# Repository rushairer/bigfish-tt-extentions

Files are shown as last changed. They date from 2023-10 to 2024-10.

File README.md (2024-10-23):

# 大鱼 TT 增强包

## 关于本项目

`大鱼TT` 是 B 站 UP`大鱼DIY`在 2023 年发布的一款 CoreXY 结构的开源 3D 打印机方案。

大家都习惯把资料在 QQ 群里讨论分享，但是不方便检索，所以我创建了这个项目，把组装过程中用到的资源，一点点收集到这里。同时也欢迎其他机友补充和提交资料。

### 简单分享下我这个零基础小白在装机过程中遇到的坑。

前前后后半个多月，学到了很多知识，感谢大鱼 DIY 给我们带来的这款大鱼 TT，感谢群里曾经帮助过我的各位朋友。

首先说 BOM 表。本来是想一键下单的，但是由于产能原因，有些店铺没货。没办法只能自己照单抓药一个个在各种店铺下单买，单品型号可能有一些差异，于是遇到了一些奇奇怪怪的问题。

我有一个树莓派 3b，装了 LED3.5 触摸屏，一直闲着。所以就打算用 BOM 里提到的树莓派+八爪鱼的方案。后来我才知道大鱼他是用小政主板做的，兼容性会比较好。八爪鱼主板遇到的一些问题基本上都是在大鱼群和八爪鱼的群里各位大佬的帮助下解决的，在这里再次表示感谢。

然后说说“拓竹”的挤出机，是所谓的 2.0 版本，尾端和散热块的地方有螺丝片加固的那款，风扇固定需要两颗 M2.5\*16 的螺丝，这个 BOM 里没有提。

再就是接近开关。一开始我是用的 BOM 链接买的 24V 的 NPN 接近开关，配的八爪鱼 1.1 主板。这个主板端是 PNP 的，所以 24V 的 NPN 不能直接用，除非自己接个下拉电阻，我不会。听说 Pro 的板子可以用 NPN。于是我又买了一块八爪鱼 Pro，实测发现即使接了 NPN 跳脚，也不能用。后来我买了一个 5V 的 NPN 常闭，可以在 1.1 和 Pro 上用，需要在 Pin 前面加上“~”。

~~关于这个接近开关问题我多提点吧，毕竟当时卡了我好几天。先说 24VNPN 的时候，我分别测试了 24V，12V，5V。在 24V 时接触金属 5.8V，不接触 3V。在 12V 时，接触金属 2.xV，不接触 1.2V。那我猜在 5V 时，接触金属应该 1.xV，不接触金属 0.xV，就可以一个 1 一个 0 两个电平形成开关信号了吧？可惜这个接近开关的额定电压是 6V-36V，在 5V 下不工作。后来我购买了 5V 的 NPN 证实了这一猜测。至于背后的原理，等我回头复习一下电路知识，重新整理。这里做个备忘。~~

6 张图来弄明白为什么八爪鱼 1.1 主板不能直接用 NPN 的接近开关，和如何解决这个问题。

图一、图二分别是 NPN 接近开关和 PNP 接近开关的原理。
通过查看八爪鱼 1.1 的电路图得知，如图四那样，接近开关的信号引脚和 GND 接了一个光耦开关。通过图三可以看到，NPN 接近开关信号引脚和 GND 之间电压很低，所以不能完全打开光耦。
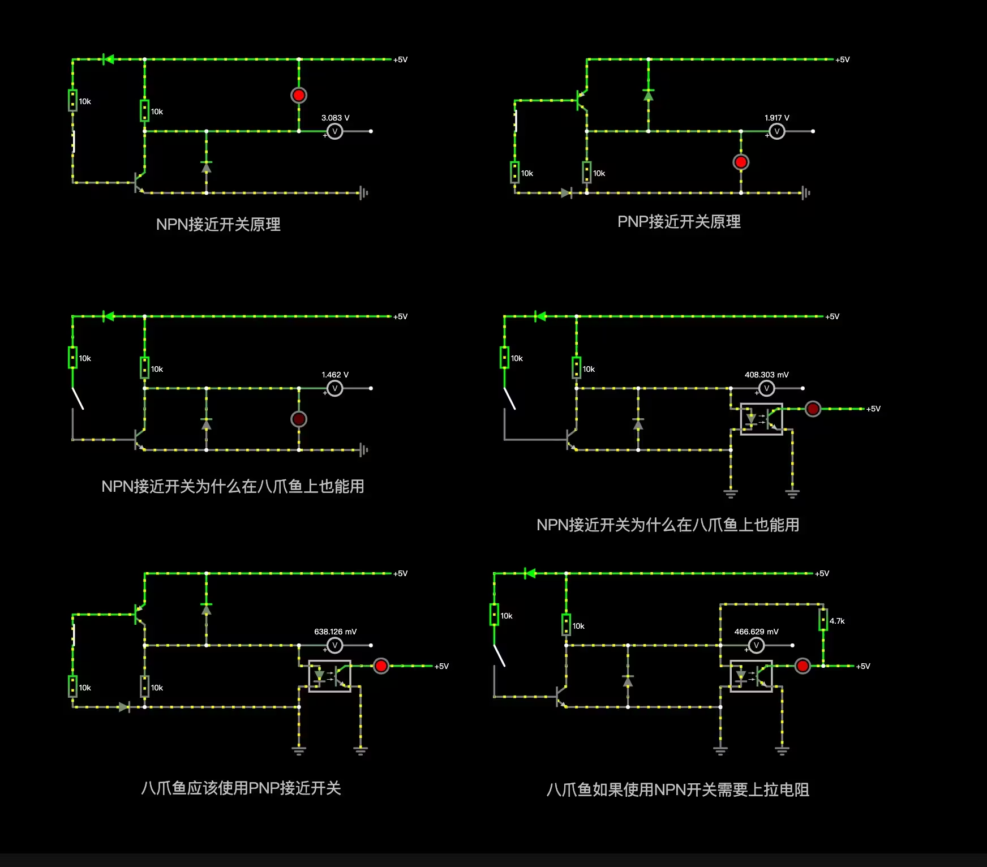
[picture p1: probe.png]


看八爪鱼的原理图，100K 下拉电阻是 NC 状态，也就没有焊。所以需要加  ~  来内部下拉，也就是 ~PB7。当光耦不能完全打开时，~PB7 的电压高低跳变就可能不稳定，所以表现出来就是不能工作或者测量不准确。具体的情况就需要看具体型号的接近开关的额定电压情况了。
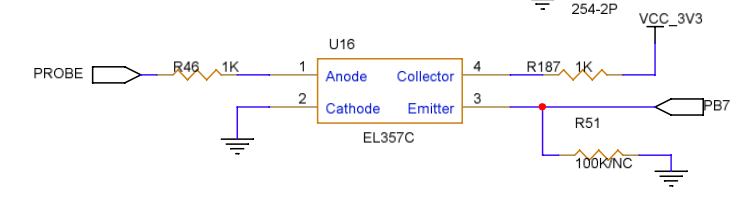
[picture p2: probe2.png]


所以我们应该用 PNP 型接近开关 或者 NPN 接近开关把信号引脚接一个上拉电阻。

~~2023 年 10 月 16 日 00:20:50 获得的好消息，24V NPN 接近开关可以在八爪鱼上使用了，接线方法：正负极接电源正负极，信号 PIN 还是接 Probe 的信号 PIN 就可以用了~~

接近开关的热飘非常明显，首层打印不稳定，所以后来我决定试试 Klicky 方案。Klicky 的开源方案有很多，我是用的 https://github.com/tanaes/whopping_Voron_mods/tree/main/pcb_klicky 的方案。停靠坞使用 MG90s/SG90 舵机，（不要用 MG996 等大电流舵机，主板带不动）。我单独开一篇来分享一下 Klicky+舵机的配置过程。

还有各种电线，是否用 CanBus，XH2.54 的端子等等细节问题。太碎了，实在是懒得一条条列举了，而且我相信列出来大家也未必一条条仔细看。还是有啥问题去群里问各位网友吧。

对了还有那个热床 MOS，如果不是大功率的热床，不需要买的。

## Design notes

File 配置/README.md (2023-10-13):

# 我的配置

## TODO

    目前没有详细说明，仅供参考。

    我把打印范围改成 300x300x300的了，周围余了5mm，不是因为Klicky，只是觉得热床很难100%四个顶点对齐，不如留点余量。

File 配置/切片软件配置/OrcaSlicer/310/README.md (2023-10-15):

# 我的配置

## 310x310x310 可以跑满吗？

我觉得我的组装精度很难保证 310x310 的四个顶点都能对应上，所以我还是改成 300x300x300 的可用区域了。

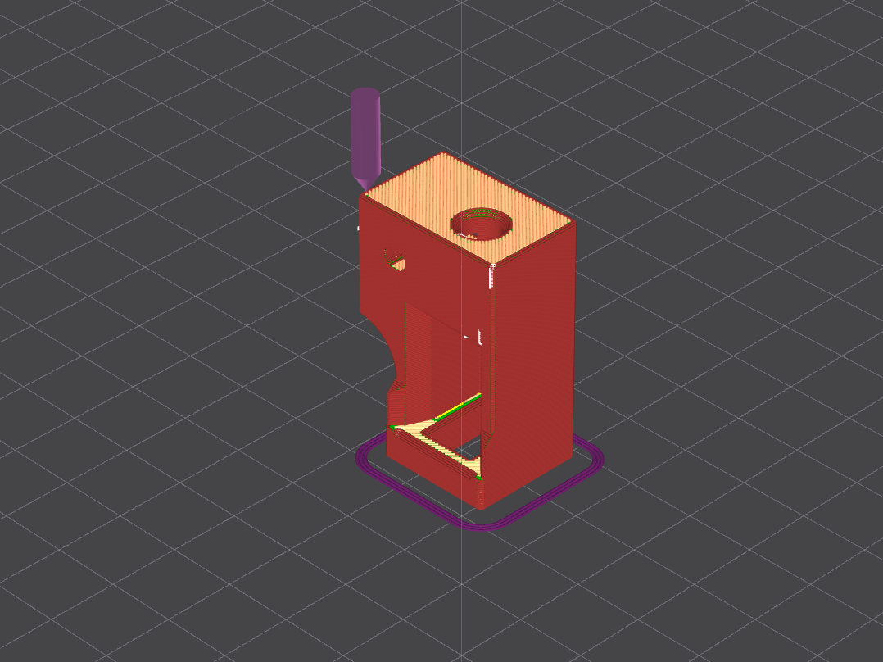
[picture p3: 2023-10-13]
扩展/Klicky/PCB Klicky/支架/切片方式-不需要支撑.png

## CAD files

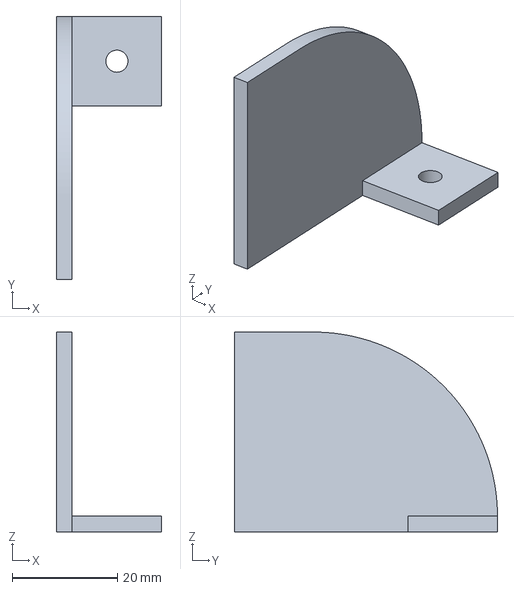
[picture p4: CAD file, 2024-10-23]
Klicky Dock 舵机扭转角度限位.3mf
20.0 x 50.0 x 38.0 mm

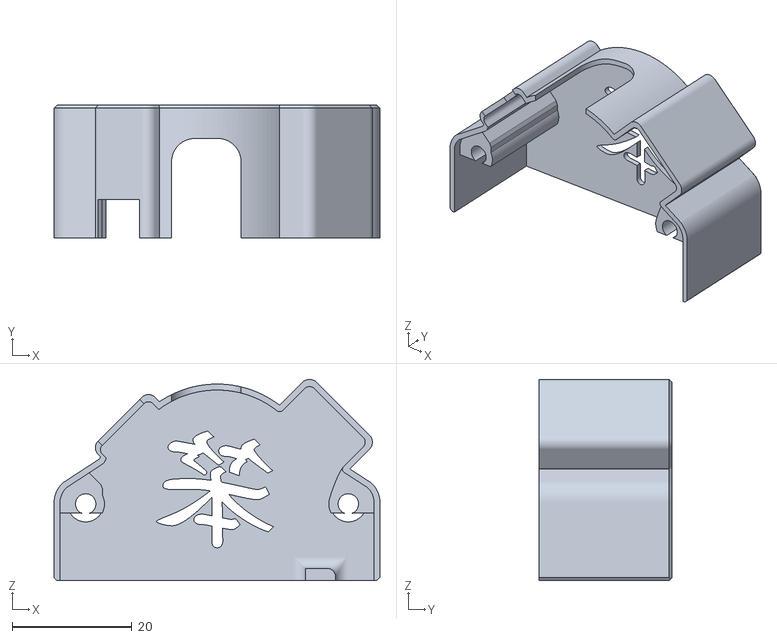
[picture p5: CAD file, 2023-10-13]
扩展/CanBus/Can 外壳.stl
54.4 x 22.2 x 33.6

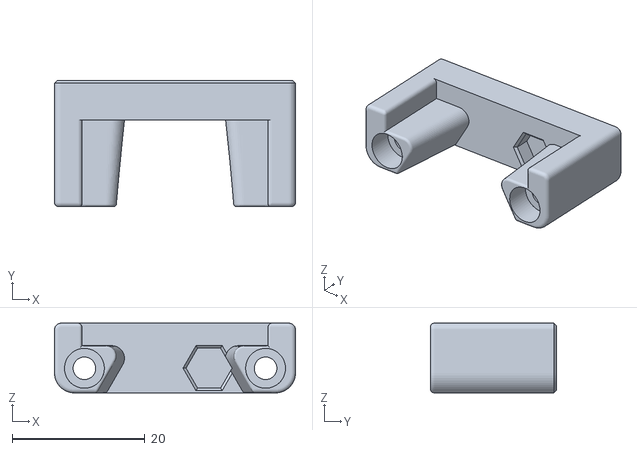
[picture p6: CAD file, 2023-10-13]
扩展/Klicky/PCB Klicky/PCB方案用的东西/停靠坞.stl
36.3 x 19.0 x 10.5

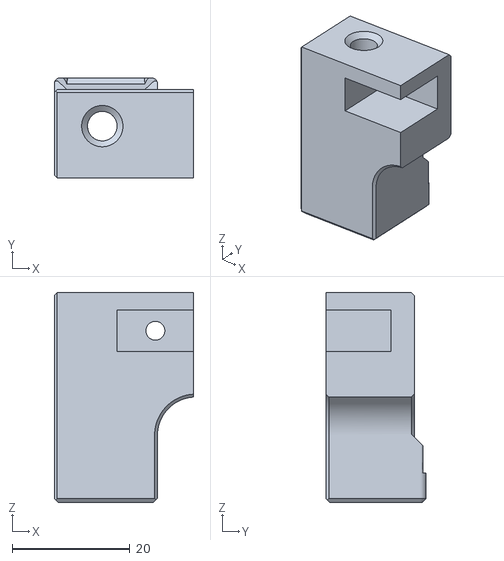
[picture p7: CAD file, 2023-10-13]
扩展/Klicky/PCB Klicky/支架/固定架-固定在原接近开关的位置.stl
23.6 x 17.0 x 35.6

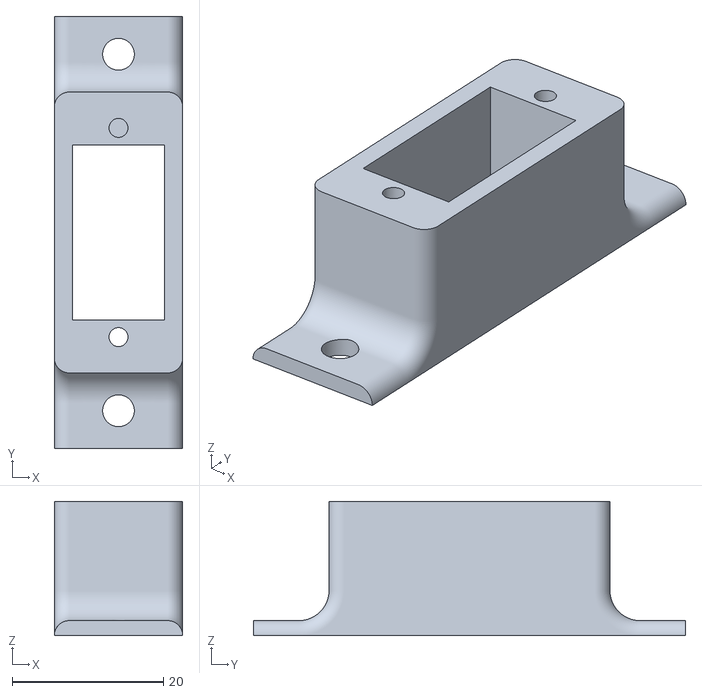
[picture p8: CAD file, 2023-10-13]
扩展/Klicky/PCB Klicky/舵机/固定在热床型材的方案/MG90s_SG90舵机固定架.stl
17.0 x 57.2 x 17.8

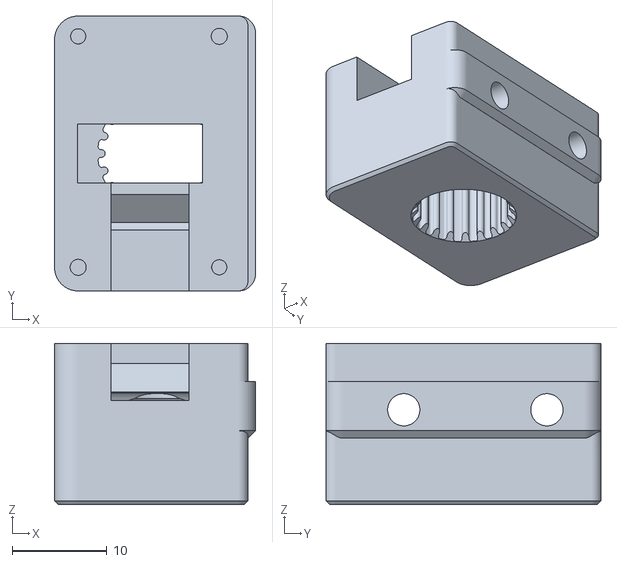
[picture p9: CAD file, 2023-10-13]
扩展/Z限位/Z轴限位PCB安装座.stl
21.2 x 29.0 x 17.0

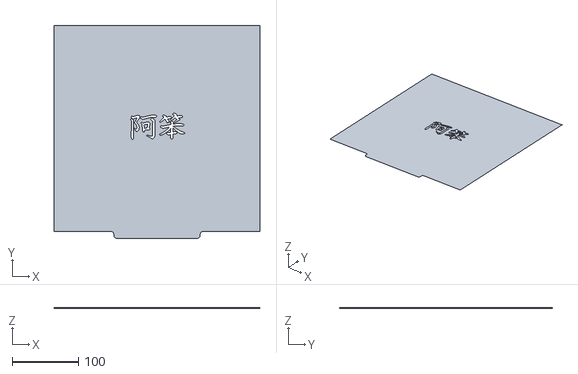
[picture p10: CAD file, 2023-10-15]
扩展/其他/310x310平台板模型.stl
310.0 x 320.0 x 0.1

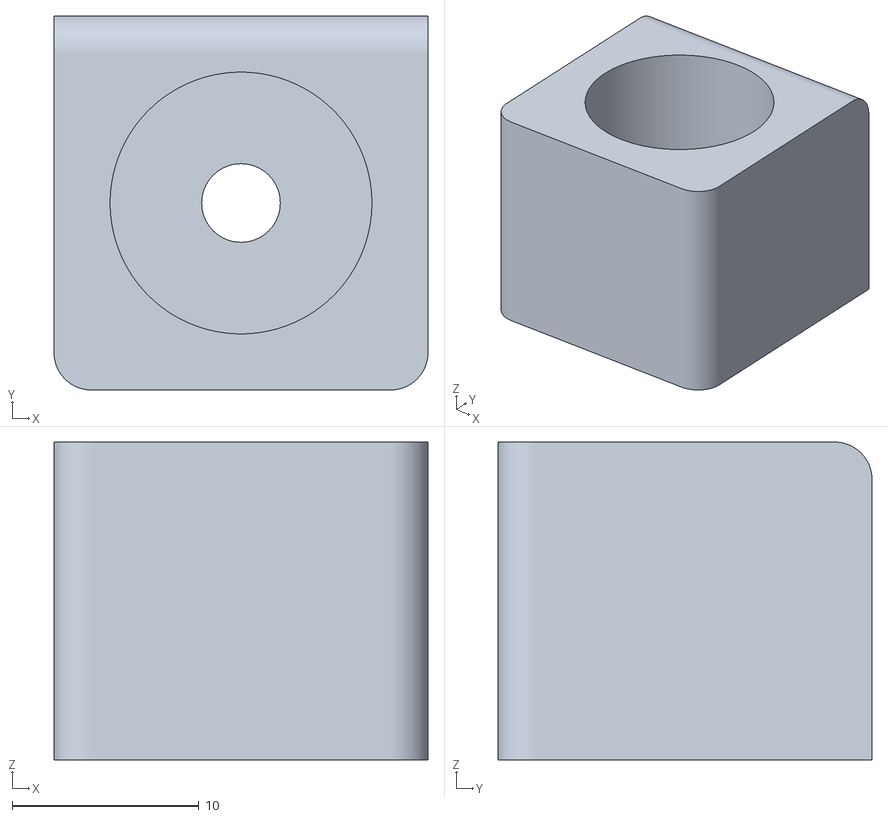
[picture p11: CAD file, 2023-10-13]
扩展/自动擦嘴/热床平台板边缘对齐辅助装置.stl
20.0 x 20.0 x 17.0

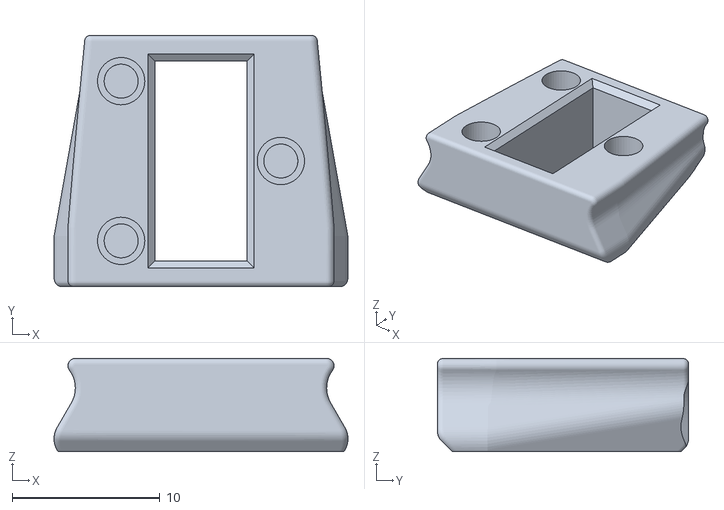
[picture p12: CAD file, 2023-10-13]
扩展/Klicky/PCB Klicky/PCB方案用的东西/热熔螺丝版探针固定架.stl
19.9 x 17.0 x 6.30

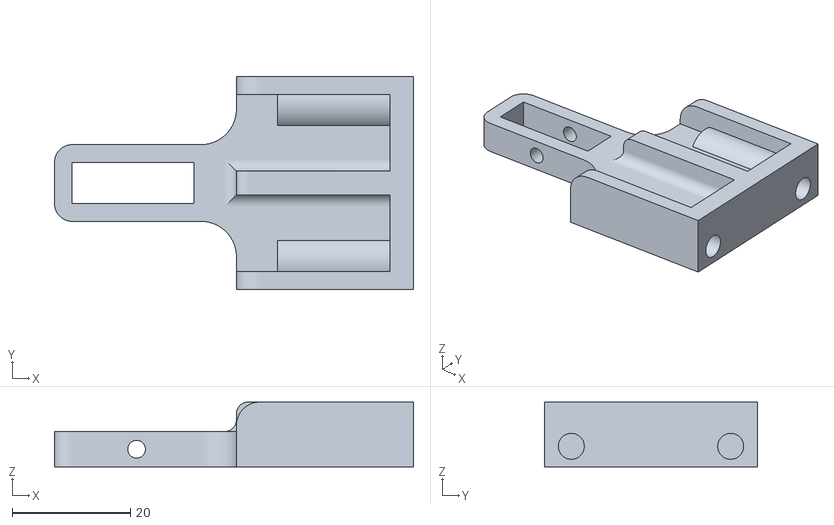
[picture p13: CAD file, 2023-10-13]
扩展/Klicky/PCB Klicky/舵机/固定在热床型材的方案/舵机齿轮连接停靠坞部分.stl
60.8 x 36.0 x 11.0

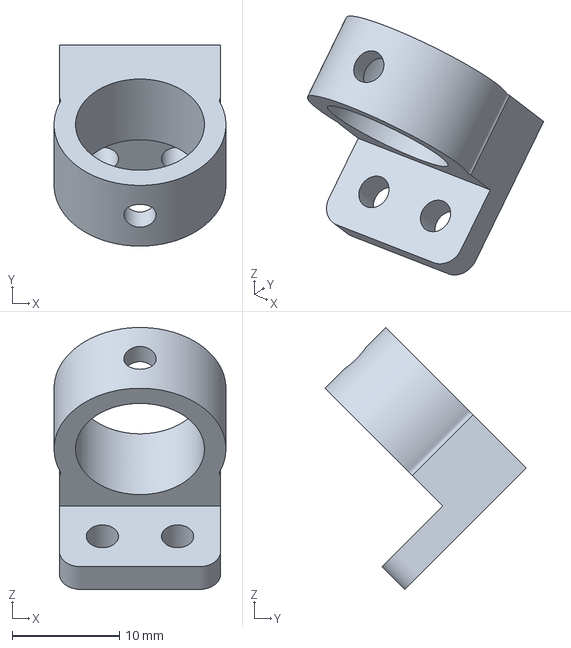
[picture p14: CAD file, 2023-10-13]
扩展/其他/大鱼TT改写字机笔架.3mf
16.0 x 18.7 x 24.4 mm

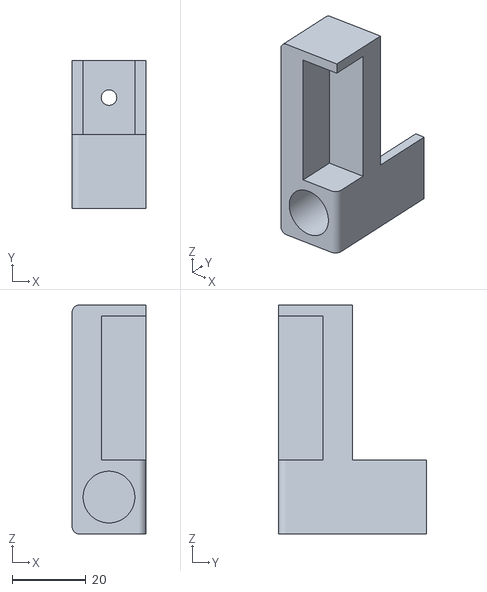
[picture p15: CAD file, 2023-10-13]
扩展/自动擦嘴/刷子头固定支架.stl
20.0 x 40.0 x 62.0

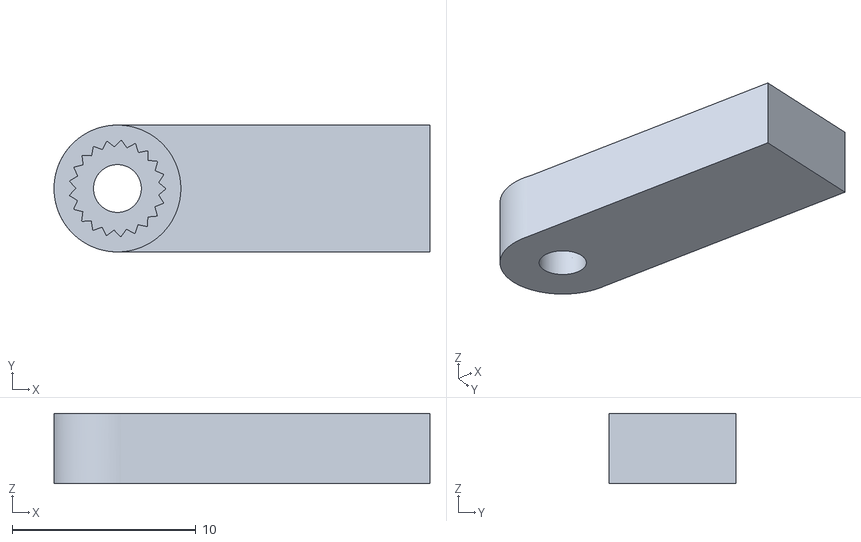
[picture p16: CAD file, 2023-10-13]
扩展/Klicky/PCB Klicky/舵机/固定在热床型材的方案/舵机齿轮.stl
20.4 x 6.90 x 3.82

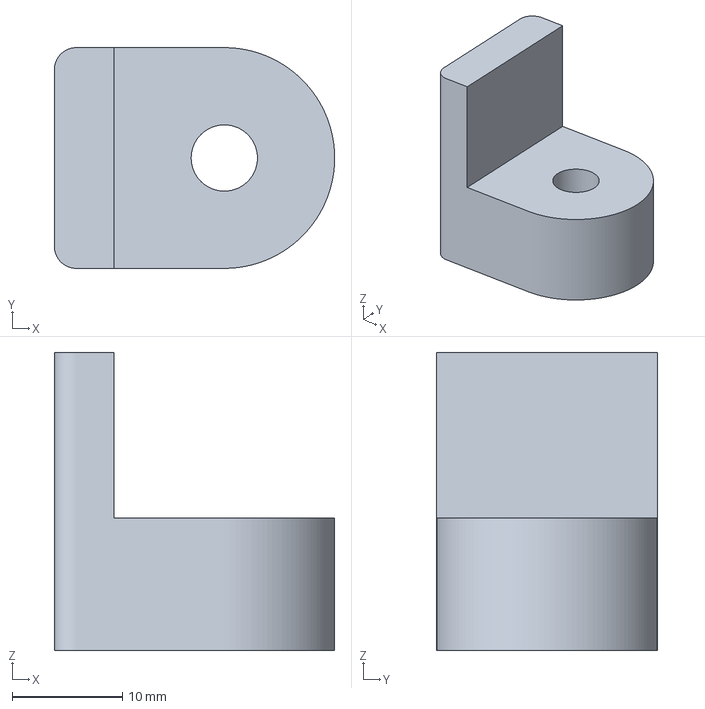
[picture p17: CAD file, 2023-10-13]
扩展/其他/四脚增高.3mf
25.4 x 20.0 x 27.0 mm

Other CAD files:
扩展/其他/电线包裹引导器.3mf
扩展/其他/丫丫版TT5015风扇支架-阿笨修改版.stl
扩展/其他/四脚.stl
扩展/其他/电源盒.stl

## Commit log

2023-10-13 feat: 分享模型
    [MG90s_SG90舵机固定架.stl, 停靠坞.stl, 刷子头固定支架.stl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]
2023-10-13 feat: 其他模型
    [Can 外壳.stl, Z轴限位PCB安装座.stl, 丫丫版TT5015风扇支架-阿笨修改版.stl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]
2023-10-15 feat: 更新了配置
    [310x310平台板模型.stl]
2023-10-15 feat: 切片软件配置
2023-10-15 feat: https://klipperscreen.readthedocs.io/en/latest/macros/#load_filament-unload_filament 提供的加载卸载耗材的代码有问题 速度太快 会卡料 换成慢速的了
2023-10-15 feat: 24V NPN 接近开关的接法更新
2024-10-23 feat: 接近开关问题补遗
    [Klicky Dock 舵机扭转角度限位.3mf]
2024-10-23 更新 README.md
